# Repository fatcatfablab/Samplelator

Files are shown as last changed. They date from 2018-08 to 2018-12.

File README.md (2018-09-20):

# Samplelator
The NYC Makerfaire 2018 FCFL exhibit will be using one or more controllers, and this area is for the code that makes it come alive!

__sketch_motor_control__

The motor used to spin the platter is controlled by this sketch. We use a Pololu Dual VNH5019 Motor Driver Shield for Arduino to generate the PWM. Note that this requires a separate microcontroller from the teensy (color sensors controller) because the motor control is somewhat independent of the midi stuff. Also, the teensy was not used since the motor control is not as timing critical in its operations.

__sketch_teensy_color__

The directory sketch_teensy_color was branched off of *sketch_colorimeter* and contains ported code to the teensy board from arduino. This sketch holds the code to read an AMS7262 6 channel color sensor. For this version, we use the Adafruit AS726x library to do the actual interfacing. The 6 channels are Violet, Blue, Green, Yellow, Orange, and Red. 

The 6 color channels can be thought of as discrete frequency spectrum of a continuous waveform. Normally, you would compare the spectrum with values from calibrated color samples in order to find the closest matching color. For this demo, we need to determine the color in a timely manner using an Teensy. So, we end up taking shortcuts to come up with the closest match. For example, we primarily use the peak channel (the channel with the strongest signal) and use that as the primary basis for selecting the color. Additionally, we use the color wheel and characteristics of the colors used in the device to come up with secondary modifications to the color matching. For example, the blue and violet colors are very close to each other in the color wheel, and have very similar peak values. However, because the blue color that we use has a stronger green component than orange, we can increase the identification between the violet color sample versus the blue color sample. Something similar happens with our yellow and red samples. Again, this is due to their proximity in the color wheel.

__sketch_channels_color__

The sketch_channels_color subdirectory was branched off of sketch_teensy_color to focus on integrating in the channel changer code.

__sketch_logo_lights__

The logo lights sketch was derived from the logo board led display of the hotshot makerfaire project. This version ditches the alternate serial port and instead uses the same usb serial port for both debug output and command input. When no command is given or active, a random command is chosen. Also added a spinning stick animation.

__sketch_break_detect__

The break detect sketch is a simple sketch to help debug the light break switch. This switch is used to detect when a color sample should be taken. It consists of an IR led plus detector, with pegs that pass in between to indicate that a sample needs to be taken. The signal received is an analog value. Hysteris is applied to the analog signal to debounce the break detection and break restoration values. This sketch was eventually incorporated in the teensy color sketch.

__sketch_analog_scope__

This utility sketch is a quick and dirty method to display the values read from an analog pin. The display is a 32 bin value, where each bin (or star) represents a value of 8. It is derived from assuming the analog pin has 256 values ranging from 0 to 255, and is divided by 8 to fit the 32 character line display. The triggerring is based off of non-zero values. Theoretically more sophisticated triggering can be added to the logic to capture certain events. This sketch was used to help debug the light break detection device.

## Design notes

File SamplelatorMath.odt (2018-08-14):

Positioning the AMS7262 6 channel color sensor for the Samplelator

# Summary

The AMS7262 sensor is an off the shelf color sensor tuned to sense 6 color channels of Violet, Blue, Green, Yellow, Orange, and Red. Most large surface materials reflect light as a range of colors, and to gain accuracy in color determination it is best to be as close to the reflected light as possible to focus on a small but stable portion of the material.

# Sensor Characteristics

From the AMS7262 specs, the field of view of the sensor aperture is a 40 degree cone (+/- 20 degrees from centerline). For example, at 25.4 mm (1 inch) distance from a sample, the radius of the cone base is tan(20 degrees) * 25.4 mm = 9.2448 mm, or a little less than 10 mm. The selection of distance depends on the overall size of the sample and the speed at which the sample moves, plus the integration time needed for the sensor to complete its sampling.

The specs for sampling of all 6 channels (which are stored on 2 bank registers) takes 2 * 2.9 ms = 5.8 ms. This value is for 1 unit of integration time. Currently, we choose 2 units of integration time, or 11.6 ms. This value was chosen by empirical means to balance the gain used (which is 64 times unity) and the integration time to get the best color readings for the smallest practical integration time. This means any stability calculations require a minimum of 11.6 ms of leeway in getting a decent color sample.

# The Samplelator Characteristics

The Samplelator uses dowels of about 36 mm diameter from which the color samples are glued to the bottoms. The maximum disk sample will then have a radius of about 18 mm. With a stationary color sample, the maximal distance that the sensor sample can be position is tan(70) * 18 mm = 49.4546 mm, or a little less than 50 mm (less than 2 inches) from the sample. Again, that calculation is at a non-moving sample.

The dowels, however, are on a rotating disk, and are located at 6 different tracks/radii. With the disk rotating at 1 complete circle very 30 seconds, each point on the disk will have a rotational speed of 2 * pi * r / 30 = pi * r / 15.

So each point at 1 meter radius will have a rotation speed of pi / 15 meters per second, or about 209 mm per second. A more useful translation would be 209 mm / 1000 mm/s = 0.209 mm per ms. With a chosen integration time of 11.6 ms, the distance a sample moves would be 11.6 ms * 0.209 mm / ms = 2.42 mm. This means the base of the cone for the sample should be reduced by at least 2.42 mm to get a stable sampling area. Rounding off to 2.5 mm, the stable sampling area at 1 meter from the center of the spinning disk is now 18 – 2.5 mm = 15.5 mm. The distance from the color sample should now be at tan(70) * 15.5 = 42.59 mm from the material at 1 meter out from center.

For 2 meters from center, the rotational speed would double at 0.418 mm / ms. The sampling radius would then be 18 – 4.84 = 13.15 mm. The maximum distance from the color sample should now be at tan(70) * 13.15 mm = 36.13 mm.

For 3 meters from center, the rotational speed would be at 0.627 mm / ms. Sampling radius at 18 – 6.27 = 11.73 mm. The maximum distance of the color sensor from the sample would be tan(70) * 11.73 = 32.23 mm.

So, a nice round-ish number would be 25.4 mm (1 inch) from the sample all the way out to 9 feet from center. This allows a safe deviation of disk wobble of +/- ¼ inch. If possible, ½ inch from the sample would be nice, though the probability of the sensor getting hit by the disk wobble increases as the distance from the sample decreases, obviously. However, this distance allow for a stable sampling to be done even at higher RPMs than 2 that is currently targetted.

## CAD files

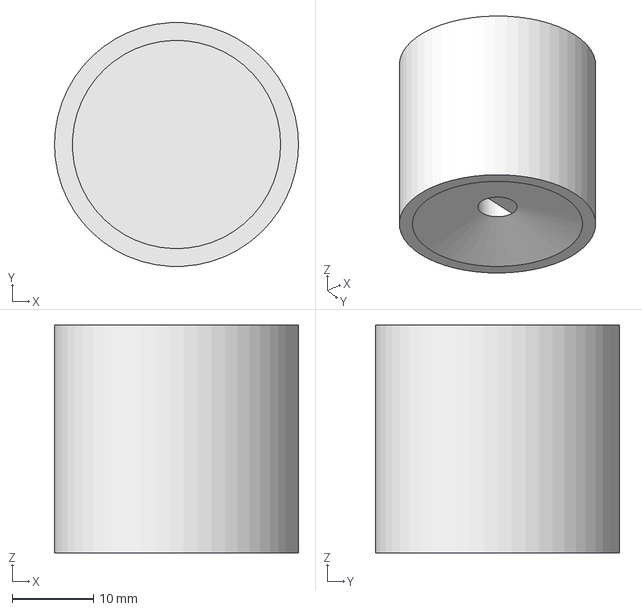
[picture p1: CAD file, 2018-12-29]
DESIGNFILES/encoderCoupler.fcstd
30.0 x 29.9 x 28.0 mm

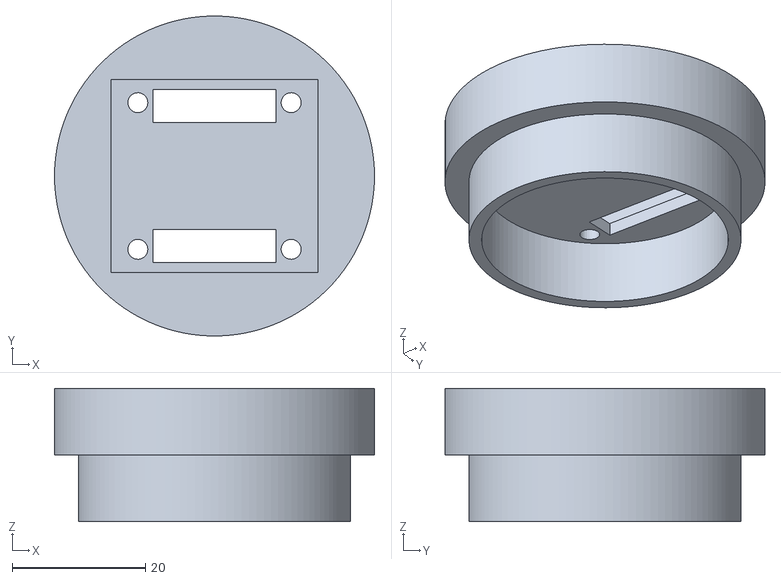
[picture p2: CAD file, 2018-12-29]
DESIGNFILES/AMS7262Base2.stl
48.0 x 48.0 x 20.0

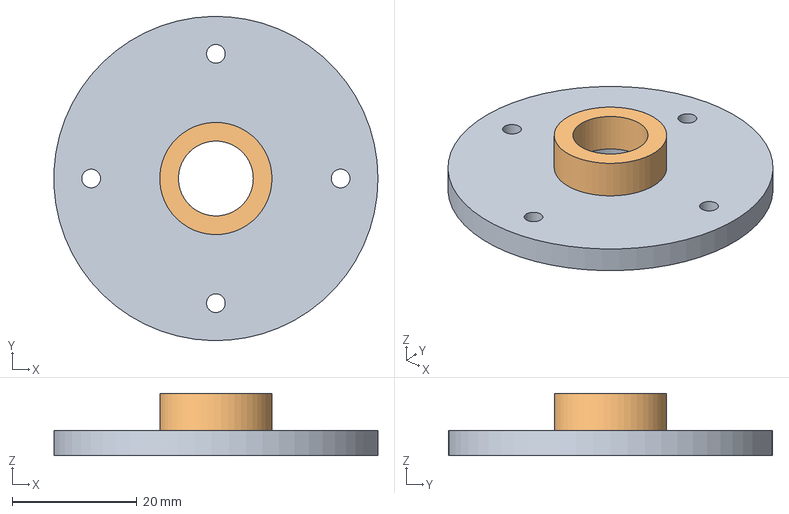
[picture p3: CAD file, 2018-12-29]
DESIGNFILES/AMS7262Cover.fcstd
52.0 x 52.0 x 10.0 mm
Plate
Hood

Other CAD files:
DESIGNFILES/AMS7262Base.fcstd
DESIGNFILES/AMS7262Cover.stl
DESIGNFILES/Sequencer_final-singlesided v36.f3d
DESIGNFILES/encoderCoupler.stl

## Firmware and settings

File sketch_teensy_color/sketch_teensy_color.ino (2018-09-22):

/***************************************************************************
   Samplelator Firmware
   Copyright 2018 Fat Cat Fab Lab, all rights reserved
   Contributors:
   - Peter Hartmann
   - Gil Nardo
   - Zack Freedman

   Hardware:
   Board: Teensy 3.6
   CPU Speed: 180MHz
   USB Mode: Serial + MIDI

   Pinout: I/O Board v1
   
   This version **does not** use neopixels as those need 5 volts.
   This uses the IR "line break" detector analog input.
   The color detection algorithm is tuned for our sample swatches.
 ***************************************************************************/

/*
   Current limited to 25mA per LED?
   We should really try 50mA
   Integration time
*/

// The pin for the external "light break" input. Note: analog pin
#define THRESHOLD_ANALOG_PIN A16

// Threshold limits of an obstacle on light break detector
int lowThreshold = 300; // 150;  // May change with timer peg and sensor relocation
int highThreshold = 500; // 500;

// After a read is initiated, a sensor needs time to perform the reading and populate the buffers.
// In UART mode, no status register is available - we just need to wait.
// Increase this if erroneous 0's are reported for some or all channels.
#define READ_TIME 30 // Milliseconds

// TEST TEST TEST: uncomment the following to not wait for start/stop signal
#define AUTOTRIGGER false

// TEST TEST TEST: uncomment to disable color to channel changes
#define NO_CHANNEL_CHANGES false

// TEST TEST TEST: uncomment one of the following for display to serial options
#define ORDER_BY_VALUE false
#define RGB_REPORT false
#define SHORT_COLOR_REPORT true

// TEST TEST TEST: uncomment for single sensor testing
#define SINGLE_SENSOR_ONLY false

// Modify this to set the integration time (must be > 1)
#define UNIT_INTEGRATE 1

#define AS726x_NUM_CHANNELS 6
#define AS726x_VIOLET 0
#define AS726x_BLUE 1
#define AS726x_GREEN 2
#define AS726x_YELLOW 3
#define AS726x_ORANGE 4
#define AS726x_RED 5

int defaultOrder[AS726x_NUM_CHANNELS] = {
  AS726x_VIOLET, AS726x_BLUE, AS726x_GREEN, AS726x_YELLOW, AS726x_ORANGE, AS726x_RED
};


// color to note assignment
int blueMidi = 36;
int greenMidi = 40;
int redMidi = 42;
int magentaMidi = 46;
int violetMidi = 48;
int yellowMidi = 50;

enum colorChannelIndex {
  violetChan = 0,
  blueChan,
  greenChan,
  yellowChan,
  redChan,
  magentaChan,
  unknownChan = 16
};

// change which channel the color gets sent to. Currently it all goes to midi channel 1
uint8_t color2Channel[] = {
  1, 1, 1, 1, 1, 1
};

uint8_t lastChannels[] = {
  1, 1, 1, 1, 1, 1
};

class ColorSensor {
  protected:
    static int allSensorIds;
    HardwareSerial & sensorPort;
    bool runCommand(char * command, bool verbose);
    bool runCommand(char * command);

  public:	// basically, this class is more like a struct+typedef
    int sensorId;
    uint16_t senseVals[AS726x_NUM_CHANNELS];
    int orderedColors[AS726x_NUM_CHANNELS];
    int totSpectrum;
    int meanSpectrum;
    int numVariance;
    int stdDevSpectrum;
    bool isReady;
    bool wasRead;
    const char *lastColor;
    int lastNote;
    int lastChan;

    ColorSensor(HardwareSerial & port);
    // ~ColorSensor(void);

    bool begin(void);
    void readColorRegs(void);
    void calcSampleStats(void);
    void printReport(const char *);
    void sendMidiOn(const char *colorInd, int useNote);
    void sendMidiOff(void);
    void calcColorMatch(void);
    void startMeasurement(void);
};

int ColorSensor::allSensorIds = 1;

ColorSensor::ColorSensor(HardwareSerial & port) : sensorPort(port) {

  sensorId = ColorSensor::allSensorIds++;
  for (int idx = 0; idx < AS726x_NUM_CHANNELS; idx++)
    senseVals[idx] = 0;
  for (int idx = 0; idx < AS726x_NUM_CHANNELS; idx++)
    orderedColors[idx] = defaultOrder[idx];
  totSpectrum = 0;
  meanSpectrum = 0;
  numVariance = 0;
  stdDevSpectrum = 0;
  isReady = false;
  wasRead = false;
  lastColor = "";
  lastNote = 0;
  lastChan = 1;
}

bool ColorSensor::runCommand(char * command, bool verbose) {
  for (byte i = 0; i < 3; i++) {
    sensorPort.println(command);

    if (sensorPort.find("OK\n")) {
      if (verbose) {
        Serial.print("Ran command ");
        Serial.println(command);
      }
      return true;
    }

    if (i != 2) {
      if (verbose) {
        Serial.print("Command ");
        Serial.print(command);
        Serial.println(" failed, retrying");
      }
      delay(5);
    }
    else if (verbose) {
      Serial.println("Command failed");
    }
  }

  return false;
}

bool ColorSensor::runCommand(char * command) {
  return runCommand(command, true);
}

bool ColorSensor::begin() {
  sensorPort.begin(115200);

  if (runCommand("AT")) Serial.println("Detected sensor");
  else Serial.println("Didn't detect sensor!!");

  if (runCommand("ATTCSMD=3") && // Switch to one-shot mode - stop continually reading
      runCommand("ATINTTIME=1") && // Set integration time to 5.6ms - read time is 2.8ms per bank
      runCommand("ATGAIN=3") && // 64x gain - required for short integration times
      runCommand("ATLEDC=00010001") && // Set LED current to 25mA for illumination and 4mA for indicator
      //runCommand("ATLEDC=00100001") && // Set LED current to 50mA for illumination and 4mA for indicator
      runCommand("ATLED1=100")) { // Turn on illuminator LED
    Serial.println("Configured successfully");
    return true;
  }
  else {
    Serial.println("Configuration failed");
    return false;
  }
}

void ColorSensor::readColorRegs(void) {
  sensorPort.println("ATDATA");

  for (byte i = 0; i < 6; i++) {
    int reading = sensorPort.parseInt();
    senseVals[i] = reading;
  }
}

// calculate some basic statistics about the current color sample
// The std dev value is also used to filter out white/black/grey colors
void ColorSensor::calcSampleStats() {
  totSpectrum = 0;
  for (int idx = 0; idx < AS726x_NUM_CHANNELS; idx++) {
    totSpectrum += senseVals[idx];
  }
  meanSpectrum = totSpectrum / AS726x_NUM_CHANNELS;
  numVariance = 0;
  for (int idx = 0; idx < 6; idx++) {
    numVariance += sq(meanSpectrum - senseVals[idx]);
  }
  stdDevSpectrum = sqrt(numVariance / (AS726x_NUM_CHANNELS - 1)); // 5 not 6 cause it's a sample

  // sort colors by value
  for (int idx = 0; idx < 5; idx++) {
    for (int jdx = idx + 1; jdx < 6; jdx++ ) {
      if (senseVals[orderedColors[idx]] < senseVals[orderedColors[jdx]]) {
        int tmpColor = orderedColors[idx];
        orderedColors[idx] = orderedColors[jdx];
        orderedColors[jdx] = tmpColor;
      }
    }
  }
}


// Report is printed to serial monitor
void ColorSensor::printReport(const char *colorInd) {
  if (ORDER_BY_VALUE) {
    Serial.print("{ id:"); Serial.print(sensorId);
    for (int idx = 0; idx < AS726x_NUM_CHANNELS; idx++) {
      switch (orderedColors[idx]) {
        case AS726x_VIOLET:
          Serial.print(", v:"); Serial.print(senseVals[AS726x_VIOLET]);
          break;
        case AS726x_BLUE:
          Serial.print(", b:"); Serial.print(senseVals[AS726x_BLUE]);
          break;
        case AS726x_GREEN:
          Serial.print(", g:"); Serial.print(senseVals[AS726x_GREEN]);
          break;
        case AS726x_YELLOW:
          Serial.print(", y:"); Serial.print(senseVals[AS726x_YELLOW]);
          break;
        case AS726x_ORANGE:
          Serial.print(", o:"); Serial.print(senseVals[AS726x_ORANGE]);
          break;
        case AS726x_RED:
          Serial.print(", r:"); Serial.print(senseVals[AS726x_RED]);
          break;
        default:
          break;
      }
    }
    Serial.print(", x:"); Serial.print(colorInd);
    Serial.println(" }");
  } // ORDER_BY_VALUE

  if (RGB_REPORT) {
    uint16_t totRgb = senseVals[AS726x_RED] + senseVals[AS726x_GREEN] + senseVals[AS726x_BLUE];
    totRgb = totRgb == 0 ? 1 : totRgb;
    uint8_t neoRed = 255 * senseVals[AS726x_RED] / totRgb;
    uint8_t neoGreen = 255 * senseVals[AS726x_GREEN] / totRgb;
    uint8_t neoBlue = 255 * senseVals[AS726x_BLUE] / totRgb;

    Serial.print("{ id:"); Serial.print(sensorId);
    Serial.print(", r:"); Serial.print(neoRed);
    Serial.print(", g:"); Serial.print(neoGreen);
    Serial.print(", b:"); Serial.print(neoBlue);
    Serial.print(", x:"); Serial.print(colorInd);
    Serial.println(" }");
  }

  if (SHORT_COLOR_REPORT) {
    // Just report the color
    Serial.print("{ id:"); Serial.print(sensorId);
    Serial.print(", x:"); Serial.print(colorInd);
    Serial.println(" }");
  }  // SHORT_COLOR_REPORT
}

void ColorSensor::sendMidiOn(const char *colorInd, int useNote) {
  printReport(colorInd);
  int useChan;
  // shortcut map the color to the configured channel
  switch (*colorInd) {
    case 'V': useChan = violetChan; break;
    case 'B': useChan = blueChan; break;
    case 'G': useChan = greenChan; break;
    case 'Y': useChan = yellowChan; break;
    case 'R': useChan = redChan; break;
    case 'M': useChan = magentaChan; break;
    default: useChan = unknownChan; useNote = 0; break;
  }
  lastColor = colorInd;
  lastNote = useNote;
  if (useChan < unknownChan)
    lastChan = color2Channel[useChan];
  else
    lastChan = unknownChan;
  if (useNote > 0) {
   //Serial.println(lastChan);
    usbMIDI.sendNoteOn(lastNote, 99, lastChan);
  } else if (useNote == 0) {
    // usbMIDI.sendNoteOn(39, 99, 1); // debug break detect
  }
}

void ColorSensor::sendMidiOff(void) {
  lastColor = "";
  if (lastNote > 0) {
    usbMIDI.sendNoteOff(lastNote, 0, lastChan);
  }
}


// Calculate the matching color (note: tuned for our sample swatches)
void ColorSensor::calcColorMatch(void) {
  if (stdDevSpectrum < 6) {
    // guess at a gray or black color
    if (!AUTOTRIGGER) {
      sendMidiOn(".", 0);
    }
    return;
  }

  // if the peak color is small, it's not a playable color
  if (senseVals[orderedColors[0]] < 75) {
    sendMidiOn(".", 0);
    return;
  }

  switch (orderedColors[0]) {
    case AS726x_VIOLET:
      if (orderedColors[1] == AS726x_BLUE) {
        sendMidiOn("Blue", blueMidi);
      } else if (orderedColors[1] == AS726x_ORANGE) {
        if (senseVals[AS726x_YELLOW] < senseVals[AS726x_RED]) {
          sendMidiOn("Magenta", magentaMidi);
          // Serial.println(millis()); // ???
        } else {
          sendMidiOn("Violet", violetMidi);
        }
      } else if (orderedColors[1] == AS726x_GREEN) {
        // sendMidiOn("Cyan", 74);
        sendMidiOn("Blue", blueMidi);
      } else {
        sendMidiOn(".", 0);
      }
      break;
    case AS726x_BLUE:
      if (orderedColors[1] == AS726x_VIOLET) {
        sendMidiOn("Blue", blueMidi);
      } else {
        sendMidiOn(".", 0);
      }
      break;
    case AS726x_GREEN:
      if (orderedColors[1] == AS726x_YELLOW && orderedColors[2] == AS726x_ORANGE) {
        sendMidiOn(".", 0);
      } else if (orderedColors[1] == AS726x_YELLOW && orderedColors[2] == AS726x_VIOLET) {
        sendMidiOn(".", 0);
      } else if (orderedColors[1] == AS726x_ORANGE) {
        sendMidiOn(".", 0);
      } else {
        sendMidiOn("Green", greenMidi);
      }
      break;
    case AS726x_YELLOW:
      if (orderedColors[2] == AS726x_VIOLET || orderedColors[2] == AS726x_BLUE ||
          orderedColors[2] == AS726x_RED) {
        sendMidiOn(".", 0);
      } else {
        sendMidiOn(".", 0);
      }
      break;
    case AS726x_ORANGE:
      if (orderedColors[1] == AS726x_GREEN && orderedColors[2] == AS726x_YELLOW) {
        sendMidiOn("Yellow", yellowMidi);
      } else if (orderedColors[1] == AS726x_VIOLET) {
        sendMidiOn("Magenta", magentaMidi);
        // Serial.println(millis());
      } else if (orderedColors[1] == AS726x_RED && orderedColors[2] == AS726x_YELLOW) {
        sendMidiOn("Red", redMidi);
      } else if (orderedColors[1] == AS726x_YELLOW) {
        if (senseVals[AS726x_GREEN] > senseVals[AS726x_RED]) {
          sendMidiOn("Yellow", yellowMidi);
        } else {
          sendMidiOn(".", 0);
        }
      } else {
        sendMidiOn(".", 0);
      }
      break;
    case AS726x_RED:
      sendMidiOn("Red", redMidi);
      break;
  }
}

void ColorSensor::startMeasurement() {
  // In UART mode, the Set Mode command initiates a one-shot reading.
  // Debug output disabled because this gets run A LOT
  runCommand("ATTCSMD=3", false);
}

ColorSensor ams[] = {
  ColorSensor(Serial1),
  ColorSensor(Serial2),
  ColorSensor(Serial3),
  ColorSensor(Serial4),
  ColorSensor(Serial5),
  ColorSensor(Serial6)
};

// State machine for loop processing
enum sensingStates {
  WAIT_START,
  INITIATE_ONE_SHOT,
  WAIT_END,
  SEND_REPORT
};

// jumpstart state machine
int readSensorState = WAIT_START;

// pins to read channel selector dials

enum dialPins {
  dialPin1 = 28,
  dialPin2 = 29,
  dialPin3 = 30//,
             //  dialPin4 = 3,
             //  dialPin5 = 4,
             //  dialPin6 = 5,
             //  dialPin7 = 6,
             //  dialPin8 = 7,
             //  dialPin9 = 8,
             //  dialPin10 = 9,
             //  dialPin11 = 10,
             //  dialPin12 = 11,
             //  dialPin13 = 12,
             //  dialPin14 = 13,
             //  dialPin15 = 14,
             //  dialPin16 = 15,
             //  dialPin17 = 16,
             //  dialPin18 = 17
};


void setup() {
  // Set up serial monitor
  Serial.begin(115200);

  delay(1000);

  // while(!Serial);

  // initialize digital pin LED_BUILTIN as an output indicator
  pinMode(LED_BUILTIN, OUTPUT);

  if (!NO_CHANNEL_CHANGES) {
    pinMode(dialPin1, INPUT_PULLUP);
    pinMode(dialPin2, INPUT_PULLUP);
    pinMode(dialPin3, INPUT_PULLUP);
    //    pinMode(dialPin4, INPUT_PULLUP);
    //    pinMode(dialPin5, INPUT_PULLUP);
    //    pinMode(dialPin6, INPUT_PULLUP);
    //    pinMode(dialPin7, INPUT_PULLUP);
    //    pinMode(dialPin8, INPUT_PULLUP);
    //    pinMode(dialPin9, INPUT_PULLUP);
    //    pinMode(dialPin10, INPUT_PULLUP);
    //    pinMode(dialPin11, INPUT_PULLUP);
    //    pinMode(dialPin12, INPUT_PULLUP);
  } // NO_CHANGE_CHANNEL

  //begin and make sure we can talk to the sensors
  Serial.println("Init AMS #0");
  for (; !ams[0].begin();) {
    Serial.println("could not connect to first sensor! Please check your wiring.");
    delay(30000);
  }
  
  if (!SINGLE_SENSOR_ONLY) {
    for (int i = 1; i < 6; i++) {
      Serial.print("Init AMS #");
      Serial.println(i + 1);

      for (; !ams[i].begin();) {
        Serial.print("could not connect to sensor #");
        Serial.print(i + 1);
        Serial.println("! Please check your wiring.");
        delay(30000);
      }
    }
  } // SINGLE_SENSOR_ONLY
 
  Serial.println("Waiting for start sample...");
}



void loop() {
  int triggerValue;

  // Serial.println(readSensorState);
  if (readSensorState == WAIT_START) {
    if (!AUTOTRIGGER) {
      triggerValue = analogRead(THRESHOLD_ANALOG_PIN);
    } else {
      triggerValue = highThreshold + 1;
    }
    // if under threshold, keep looking
    if (triggerValue > highThreshold) {
      ams[0].isReady = false;
      ams[0].wasRead = false;
      ams[0].sendMidiOff();
      if (!SINGLE_SENSOR_ONLY) {
        for (int i = 1; i < 6; i++) {
          ams[i].isReady = false;
          ams[i].wasRead = false;
          ams[i].sendMidiOff();
        }
      } else {
        for (int i = 1; i < 6; i++) {
          ams[i].isReady = true;
          ams[i].wasRead = true;
        }
      } // SINGLE_SENSOR_ONLY
      readSensorState = INITIATE_ONE_SHOT;
      digitalWrite(LED_BUILTIN, HIGH);
    } else {
      // Serial.print("Wait Start : "); Serial.println(triggerValue);
    }
  }

  if (readSensorState == INITIATE_ONE_SHOT) {
    ams[0].startMeasurement(); // initiate one shot color sensing
    if (!SINGLE_SENSOR_ONLY) {
      for (int i = 1; i < 6; i++) {
        ams[i].startMeasurement();
      }
    } // SINGLE_SENSOR_ONLY
    delay(READ_TIME); // Hardcoded delay - no dataReady() available for UART
    readSensorState = SEND_REPORT;
  }

  if (readSensorState == SEND_REPORT) {
    ams[0].readColorRegs();
    if (!SINGLE_SENSOR_ONLY) {
      for (int i = 1; i < 6; i++) {
        ams[i].readColorRegs();
      }
    }

    ams[0].calcSampleStats();
    ams[0].calcColorMatch();
    if (!SINGLE_SENSOR_ONLY) {
      for (int i = 1; i < 6; i++) {
        ams[i].calcSampleStats();
        ams[i].calcColorMatch();
      }
    } // SINGLE_SENSOR_ONLY
    readSensorState = WAIT_END;
  }

  if (readSensorState == WAIT_END) {
    if (!AUTOTRIGGER) {
      triggerValue = analogRead(THRESHOLD_ANALOG_PIN);
    } else {
      triggerValue = lowThreshold - 1;
    }
    if (triggerValue < lowThreshold) {
      readSensorState = WAIT_START;
      digitalWrite(LED_BUILTIN, LOW);

      if (!NO_CHANNEL_CHANGES) {
        // read the color to channel switches here
        int dialCode = digitalRead(dialPin1) + digitalRead(dialPin2) * 2 + digitalRead(dialPin3) * 4;
        //        int dialCode_v = digitalRead(dialPin1) + digitalRead(dialPin2) * 2 + digitalRead(dialPin3) * 4;
        //        int dialCode_b = digitalRead(dialPin4) + digitalRead(dialPin5) * 2 + digitalRead(dialPin6) * 4;
        //        int dialCode_g = digitalRead(dialPin7) + digitalRead(dialPin8) * 2 + digitalRead(dialPin9) * 4;
        //        int dialCode_y = digitalRead(dialPin10) + digitalRead(dialPin11) * 2 + digitalRead(dialPin12) * 4;
        //        int dialCode_r = digitalRead(dialPin13) + digitalRead(dialPin14) * 2 + digitalRead(dialPin15) * 4;
        //        int dialCode_m = digitalRead(dialPin16) + digitalRead(dialPin17) * 2 + digitalRead(dialPin18) * 4;

        switch (dialCode) {
          case 1: {
              color2Channel[violetChan] = 2;
              color2Channel[blueChan] = 2;
              color2Channel[greenChan] = 2;
              color2Channel[yellowChan] = 2;
              color2Channel[redChan] = 2;
              color2Channel[magentaChan] = 2;
              break;
            }

          case 2: {
              color2Channel[violetChan] = 3;
              color2Channel[blueChan] = 3;
              color2Channel[greenChan] = 3;
              color2Channel[yellowChan] = 3;
              color2Channel[redChan] = 3;
              color2Channel[magentaChan] = 3;
              break;
            }

          case 4: {
              color2Channel[violetChan] = 4;
              color2Channel[blueChan] = 4;
              color2Channel[greenChan] = 4;
              color2Channel[yellowChan] = 4;
              color2Channel[redChan] = 4;
              color2Channel[magentaChan] = 4;
              break;
            }

          default: {
              color2Channel[violetChan] = 1;
              color2Channel[blueChan] = 1;
              color2Channel[greenChan] = 1;
              color2Channel[yellowChan] = 1;
              color2Channel[redChan] = 1;
              color2Channel[magentaChan] = 1;
            }
        }

        //        switch (dialCode_v) {
        //          case 1: color2Channel[violetChan] = 2; break;
        //          case 2: color2Channel[violetChan] = 3; break;
        //          case 4: color2Channel[violetChan] = 4; break;
        //          default:
        //            color2Channel[violetChan] = 1;
        //        }
        //        switch (dialCode_b) {
        //          case 1: color2Channel[blueChan] = 2; break;
        //          case 2: color2Channel[blueChan] = 3; break;
        //          case 4: color2Channel[blueChan] = 4; break;
        //          default:
        //            color2Channel[blueChan] = 1;
        //        }
        //        switch (dialCode_g) {
        //          case 1: color2Channel[greenChan] = 2; break;
        //          case 2: color2Channel[greenChan] = 3; break;
        //          case 4: color2Channel[greenChan] = 4; break;
        //          default:
        //            color2Channel[greenChan] = 1;
        //        }
        //        switch (dialCode_y) {
        //          case 1: color2Channel[yellowChan] = 2; break;
        //          case 2: color2Channel[yellowChan] = 3; break;
        //          case 4: color2Channel[yellowChan] = 4; break;
        //          default:
        //            color2Channel[yellowChan] = 1;
        //        }
        //        switch (dialCode_r) {
        //          case 1: color2Channel[redChan] = 2; break;
        //          case 2: color2Channel[redChan] = 3; break;
        //          case 4: color2Channel[redChan] = 4; break;
        //          default:
        //            color2Channel[redChan] = 1;
        //        }
        //        switch (dialCode_m) {
        //          case 1: color2Channel[magentaChan] = 2; break;
        //          case 2: color2Channel[magentaChan] = 3; break;
        //          case 4: color2Channel[magentaChan] = 4; break;
        //          default:
        //            color2Channel[magentaChan] = 1;
        //      }
      } // NO_CHANGE_CHANNEL
    } else {
      // Serial.print("Wait End : "); Serial.println(triggerValue);
    }
  }
}

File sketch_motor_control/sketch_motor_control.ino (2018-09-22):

/*
 * Samplelator speed control, using Arduino Mega (Adjusted PWN FREQ!!).
*/

#include "DualVNH5019MotorShield.h"

// FIXME: for single motor, not sure about both PWMs becoming the same, i.e., pin 9
DualVNH5019MotorShield motor(2, 7, 9, 6, A0, 2, 7, 9, 12, A1);
// DualVNH5019MotorShield motor(2, 4, 9, 6, A0, 7, 8, 10, 12, A1); // default values
// DualVNH5019MotorShield motor; // default

#define MINMOTOR_VALUE 0
#define MAXMOTOR_VALUE 400
#define MINPOT_VALUE 0
#define MAXPOT_VALUE 1023

// change this value to the highest speed you want to give the motor controller
#define MAXSPEED_MOTOR MAX_MOTOR_VALUE

// change this value to the amount of speed changes per loop()
#define MAXDELTA_SPEED 5

// Change this value to larger values to see blink for faster processors
// #define MAXBLINK_INTERVAL 10000    // For Teensy 3.6
#define MAXBLINK_INTERVAL 10    // For Arduino Uno

int speedPin = A3;    // select the input pin for the potentiometer
int ledPin = 13;      // select the pin for the LED
  // Pin 13: Arduino has an LED connected on pin 13
  // Pin 11: Teensy 2.0 has the LED on pin 11
  // Pin  6: Teensy++ 2.0 has the LED on pin 6
  // Pin 13: Teensy 3.0 has the LED on pin 13
int blinkInterval = 0;
int blinkState = 0;

int rampSpeed = 0;
int matchedGoal = 0;
unsigned char got1Fault = 0;
unsigned char got2Fault = 0;


void setup() {
  TCCR2B = (TCCR2B & 0b11111000) | 0x01;
 
   // declare the ledPin as an OUTPUT:
  pinMode(ledPin, OUTPUT);
  Serial.begin(115200); 
  motor.init(); 
}


// Report any motor faults and delay till fault disappears
// Note: even though we modified the board as a single motor driver, the docs
//       says to monitor both half-bridge status to determine fault status
void delayIfFault() {
  unsigned char check1 = motor.getM1Fault();
  unsigned char check2 = motor.getM2Fault();
  if (check1 && !got1Fault) {
    Serial.println("Motor 1 fault");
  }
  if (check2 && !got2Fault) {
    Serial.println("Motor 2 fault");
  }
  if (got1Fault && !check1) {
    Serial.println("Motor 1 clear");
  }
  if (got2Fault && !check2) {
    Serial.println("Motor 2 clear");
  }
  if (check1 || check2) {
    // sleep 60secs if a motor has a fault
    for (int idx = 0; idx < 60; idx++)
      delay(1000);
  } else {
    // delay between motor speed commands
    delay(2);
  }
  got1Fault = check1;
  got2Fault = check2;
}


void loop() {
  
  blinkInterval++;
  if (blinkInterval > MAXBLINK_INTERVAL) {
    blinkInterval = 0;
    blinkState = !blinkState;
    if (blinkState)
      digitalWrite(ledPin, HIGH);
    else
      digitalWrite(ledPin, LOW);
  }

  if (got1Fault || got2Fault) {
    delayIfFault();
    return;
  }

  unsigned int speedChange;
  unsigned int wantSpeed = analogRead(speedPin);
  if (abs(rampSpeed - wantSpeed) < MAXDELTA_SPEED) {
    // reduce chatter
    if (matchedGoal < 1000) {
      matchedGoal++;
      return;
    }
    matchedGoal = 0;
    rampSpeed = wantSpeed;
  } else if (rampSpeed < wantSpeed) {
    speedChange = (wantSpeed - rampSpeed) / 2;
    speedChange = (MAXDELTA_SPEED < speedChange) ? MAXDELTA_SPEED : speedChange;
    rampSpeed += speedChange;
  } else if (rampSpeed > wantSpeed) {
    speedChange = (rampSpeed - wantSpeed) / 2;
    speedChange = (MAXDELTA_SPEED < speedChange) ? MAXDELTA_SPEED : speedChange;
    if (rampSpeed > wantSpeed * 2) {
      // apply some brake if significantly slowing down
      motor.setM1Brake(MAXDELTA_SPEED);
    }
    rampSpeed -= speedChange;
  }
 
  int motorSpeed;

  if (rampSpeed < MINPOT_VALUE) {
    motorSpeed = MINMOTOR_VALUE;
  } else if (rampSpeed > MAXPOT_VALUE) {
    motorSpeed = MAXMOTOR_VALUE;
  } else {
    motorSpeed = map(rampSpeed, MINPOT_VALUE, MAXPOT_VALUE, MINMOTOR_VALUE, MAXMOTOR_VALUE);
  }
  //  Serial.print("motorSpeed="); Serial.println(motorSpeed);
  if (motorSpeed == 0) {
    // apply brakes
    motor.setM1Brake(MAXDELTA_SPEED);
  } else {
    motor.setM1Speed(motorSpeed); // Note: we only send commands to M1, but actually control both
  }

  delayIfFault();
}

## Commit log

2018-08-12 Prototype color sensor driver
2018-08-14 Add sensor distance calculations document
2018-08-18 ported to teensy from arduino
2018-08-20 utility sketches to debug light break switch
2018-08-26 motor control sketch added
2018-08-27 Add tuning for motor control
2018-09-04 change to single motor control mods
2018-09-17 use minimal brakes, map pot to motor speed
2018-09-17 add printing raw integer value of analog pin
2018-09-19 branched channel changing from teensy color
2018-09-20 Added UART driver test sketch
2018-09-20 Formatting changes
    Auto-formatted, replaced ifdefs with switching statements for code
    readability
    [sketch_teensy_color.ino]
2018-09-20 change to single channel selector switch
2018-09-20 Implemented serial driver code and new pin layout
2018-09-20 Switched from six dials to one
2018-09-20 change PWM freq to 30K
2018-09-20 Sensor 1 is now initialized first
2018-09-22 added screwdown terminal on A3
2018-10-18 add Fusion360 file
    [Sequencer_final-singlesided v36.f3d]
2018-12-29 Freecad/STL files for AMS7262 adafruit module
    These are the design files for the Adafruit AMS7262 color module holder. These sit on top of PVC pipes that are cut to keep the face of the module to within 1/4 of an inch of the rotating disk bottom. The tolerance is very tight so be careful to make the bottom of the platter as flat as possible. The cover is not necessary but may cut down on stray ambient light from confusing the color reading. Note: there is no AMS7262Base1.stl file, just use the 'Base2 file.
    [AMS7262Base.fcstd, AMS7262Base2.stl, AMS7262Cover.fcstd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]
2018-12-29 Couples the speed switch (rod portion) to the pot
    The large speed switch pivot is a rod that attaches to a potentiometer at one of the ends using this 3D part.
    [encoderCoupler.fcstd, encoderCoupler.stl]
